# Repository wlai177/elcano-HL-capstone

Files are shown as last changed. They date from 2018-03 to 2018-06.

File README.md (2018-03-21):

View this project on [CADLAB.io](https://cadlab.io/node/765). 

# elcano-HL-capstone
Repo for the Elcano high-level redesign project (BEE capstone project)

The Elcano High-Level system is responsible for setting a desired vehicle speed and direction based on localization, pathfinding, and obstacle detection. The Low-Level system then has the job of making the vehicle execute the desired commands. At present, the High-Level system is partitioned among several processors:
· C7 (Raspberry Pi) processes visual information
· C6 (Arduino Mega) localization based on GPS, speed, and INU
· C5 (Arduino Micro) Lidar/sonar obstacle detection
· C4 (Arduino Mega) computes path from digital map
· C3 (Arduino Micro) processes all data and sends instructions to Low-Level

The High-Level Redesign project seeks to port the C6, C4, and C3 processors to a single Arduino DUE. The new processor is designated as the C643 processor and has the following features:
· Elcano Low-Level Backwards Compatibility
· Simplified Serial Communication
· Single Processor Operation
· Arduino IDE Friendly
· Smaller Footprint
· CAN Bus Support
· 32-bit processing

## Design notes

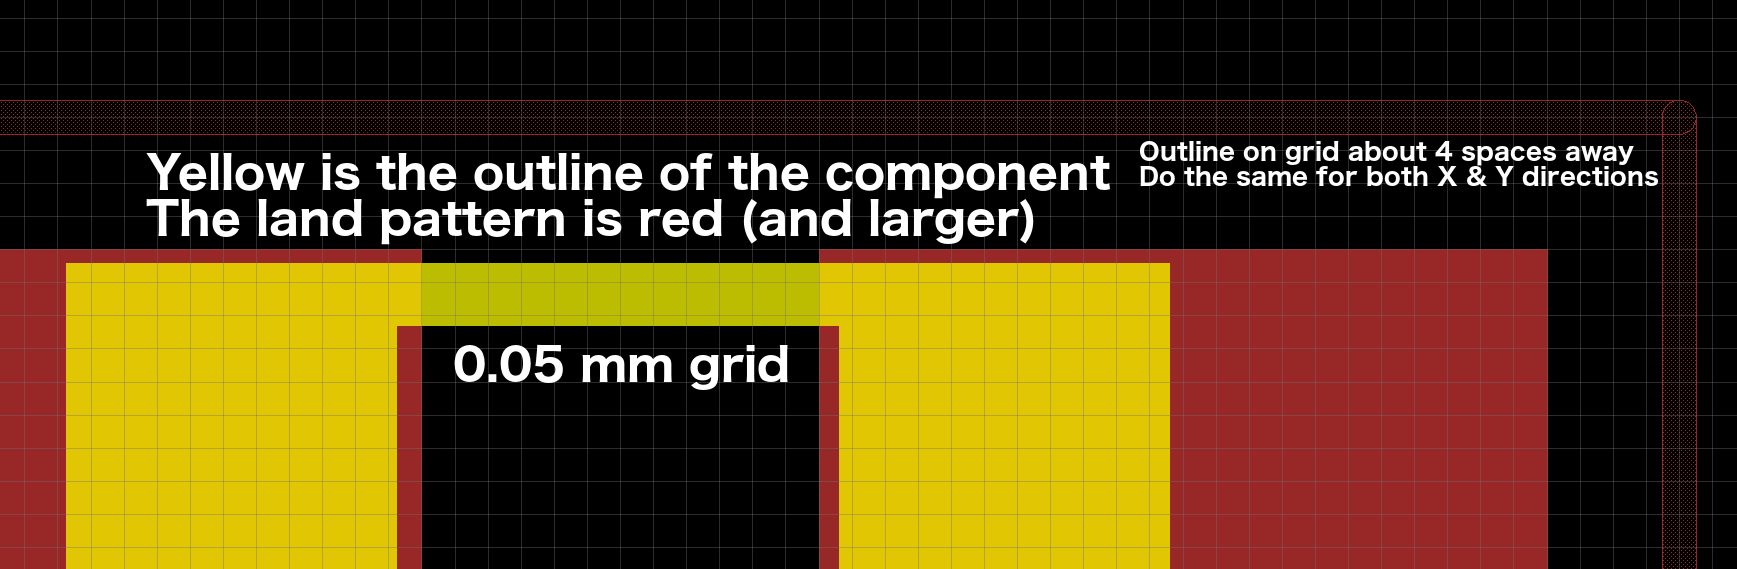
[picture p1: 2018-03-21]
hardware/EAGLE/New Eagle Libraries/SparkFun-Eagle-Libraries-master/images/CourtyardExcess.png

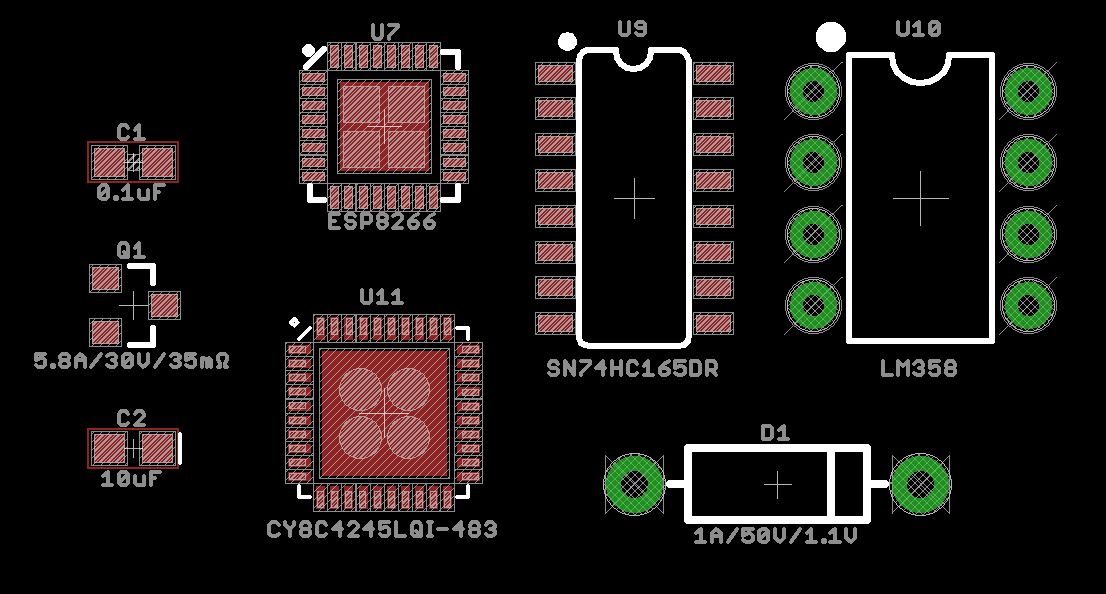
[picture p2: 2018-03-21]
hardware/EAGLE/New Eagle Libraries/SparkFun-Eagle-Libraries-master/images/FootprintExample.png

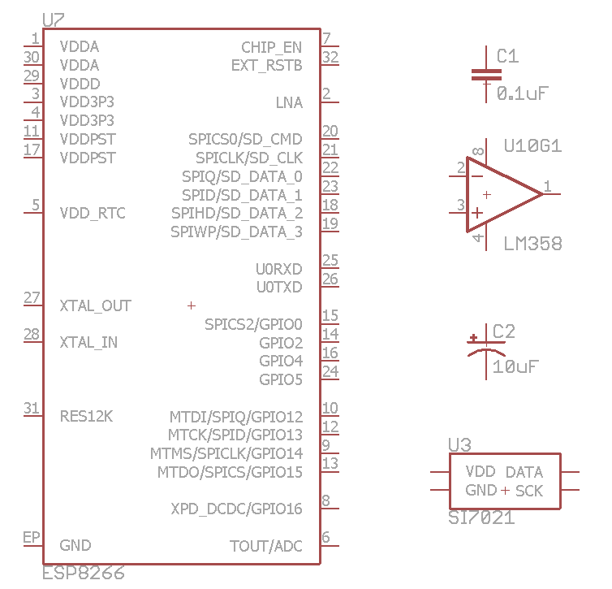
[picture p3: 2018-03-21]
hardware/EAGLE/New Eagle Libraries/SparkFun-Eagle-Libraries-master/images/SymbolExample.png

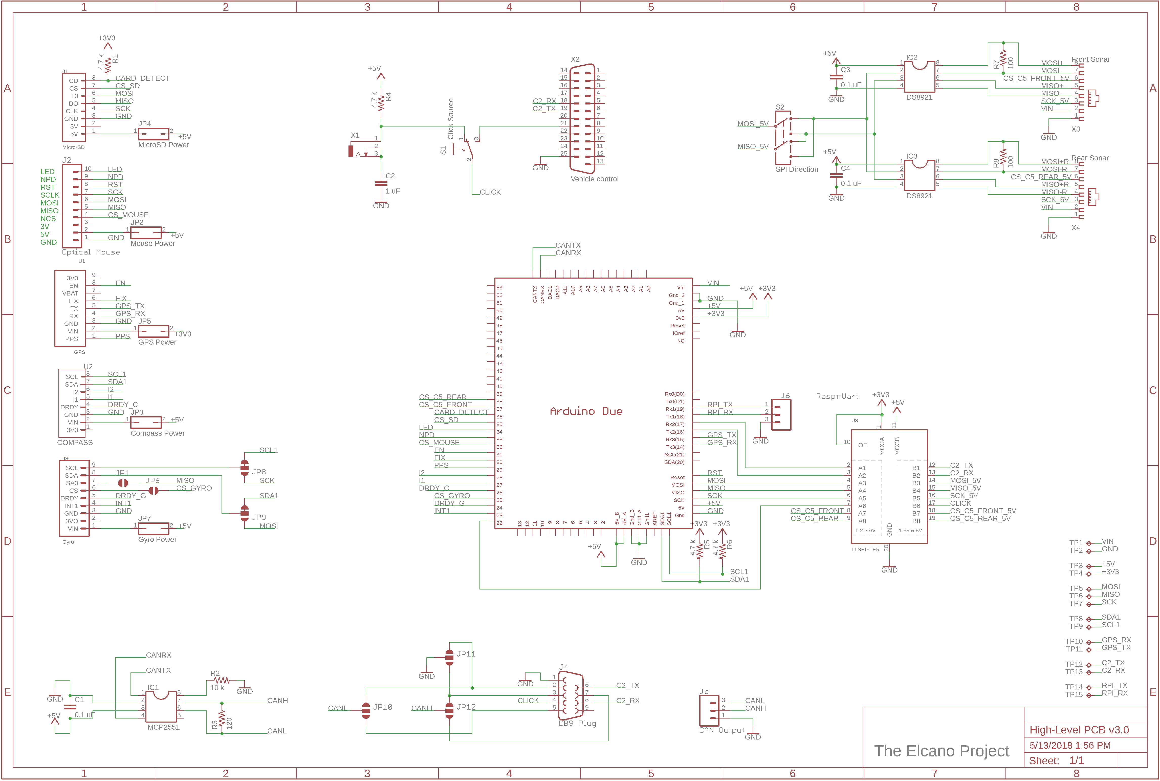
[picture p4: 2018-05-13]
hardware/HL v3 sch - May 13.png

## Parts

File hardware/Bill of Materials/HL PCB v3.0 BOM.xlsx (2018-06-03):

 | Elcano High-Level Bill of Materails
 | High-level PCB v3.0
 | 2018-06-01
# | Item | Value | Quantity | Reference Designator | Notes
1 | Resistor | 4.7 kΩ | 4 | R1 R4 R5 R6
2 | Resistor | 10 kΩ | 1 | R2
3 | Resistor | 120 Ω | 1 | R3 | Optional depending on CAN bus application
4 | Resistor | 100 Ω | 2 | R7 R8
5 | Capacitor | 0.1 uF | 3 | C1 C3 C4
6 | Capacitor | 1 uF | 1 | C2
7 | MCP2551 | - | 1 | IC1 | CAN Bus tranciever
8 | DS8921 | - | 1 | IC2 IC3 | Differential Line Driver and Receiver Pair
9 | Arduino Due | - | 1 | - | https://store.arduino.cc/usa/arduino-due
10 | MicroSD Breakout | - | 1 | J1 | https://www.adafruit.com/product/254
11 | Optical Mouse Sensor | - | 1 | J2 | http://ardupilot.org/copter/docs/common-mouse-based-optical-flow-sensor-adns3080.html
12 | GPS Breakout | - | 1 | U1 | https://www.adafruit.com/product/746
13 | Compass Breakout | - | 1 | U2 | https://www.adafruit.com/product/1120
14 | Gyro Breakout | - | 1 | J3 | https://www.adafruit.com/product/1032
15 | TXS0108E Breakout | - | 1 | - | Logic Level Shifter (5V to 3.3V)
16 | DB9 Male Connector | - | 1 | J4
17 | DB25 Male Connector | - | 1 | X2
18 | 2.5mm Audio Jack | - | 1 | X1
19 | Phoenix Terminal Connector | - | 1 | J5 | Three terminal
20 | RJ45 Connector | - | 2 | X3 X4
21 | SPDT Switch | - | 1 | S1
22 | DPDT Switch | - | 1 | S2
23 | Test Points | - | 15 | TP1-15
24 | MicroSD Card | - | 1 | -
25 | GPS SMA to uFL Adapter | - | 1 | - | Optional
26 | GPS Antenna | - | 1 | - | Optional
27 | Jumpers | - | 5 | -
28 | Female Headers | - | As Required | -
29 | Male Headers | - | As Required | -
30 | 2 Row Headers | - | As Required | -
31 | IC Sockets | - | 3 | -
32 | 7/16" Standoff | - | 8 | -
33 | #2-56 Nuts | - | 8 | -
34 | #2-56 x 3/4 Screws | - | 8 | -

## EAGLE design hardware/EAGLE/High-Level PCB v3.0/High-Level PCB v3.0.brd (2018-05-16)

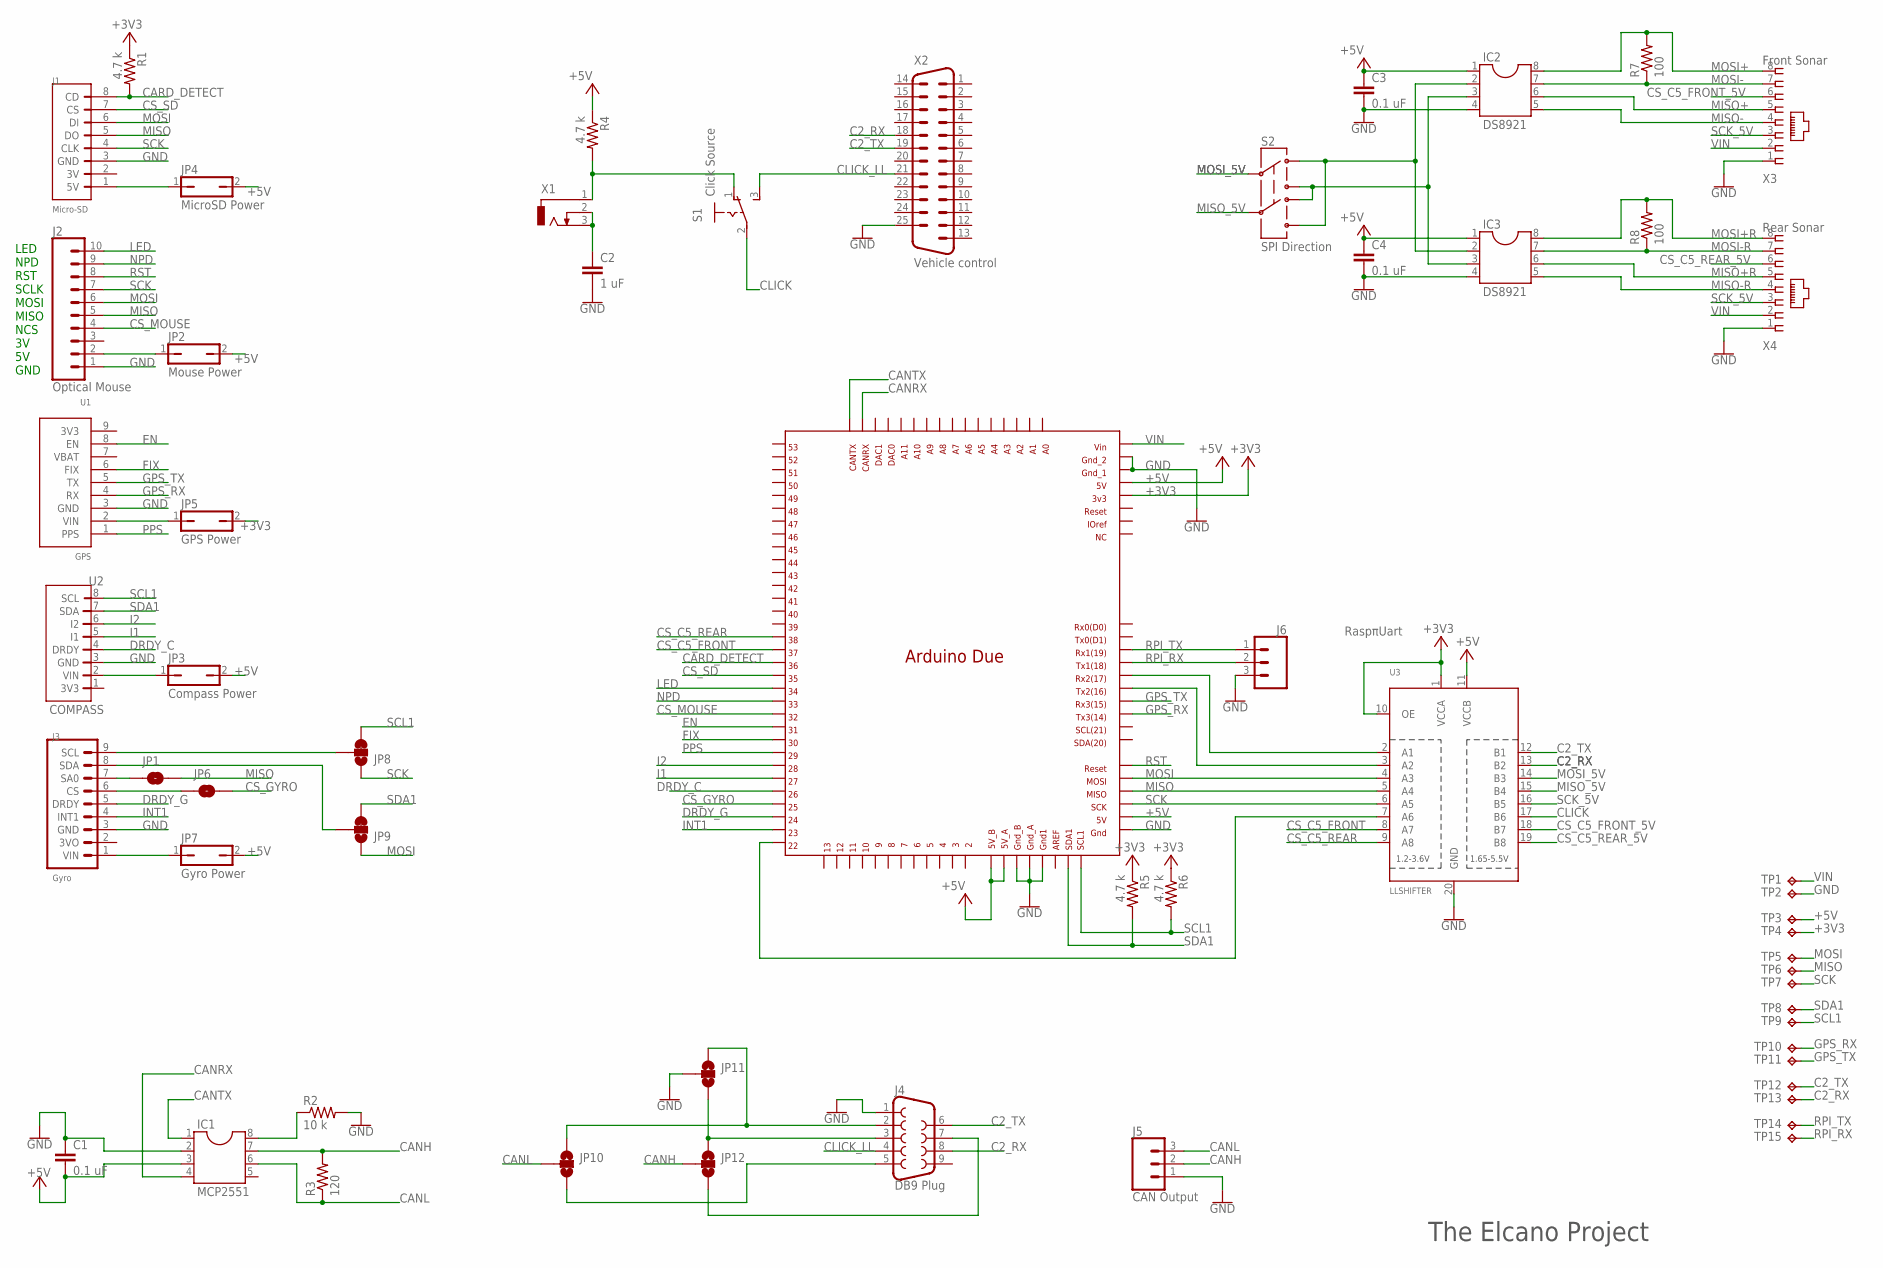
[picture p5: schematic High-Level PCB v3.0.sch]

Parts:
C1, C3, C4: 0.1 uF; C2.5-5
C2: 1 uF; C2.5-5
IC1: MCP2551; DIL08
IC2, IC3: DS8921; DIL08
J1: Micro-SD; ELSDCARD
J2: Optical Mouse; 1X10
J3: Gyro; ELGYRO
J4: DB9 Plug; DB9_MALE
J5: CAN Output; SCREWTERMINAL-5MM-3
J6: RaspπUart; 1X03
JP1, JP6: JUMPER-SMT_2_NO_SILK; SMT-JUMPER_2_NO_SILK
JP2: Mouse Power; JP1
JP3: Compass Power; JP1
JP4: MicroSD Power; JP1
JP5: GPS Power; JP1
JP7: Gyro Power; JP1
JP8, JP9: JUMPER-SMT_3_1-NC_TRACE_SILK; SMT-JUMPER_3_1-NC_TRACE_SILK
JP10, JP11, JP12: JUMPER-SMT_3_NO_SILK; SMT-JUMPER_3_NO_SILK
MCU1: DUE(NORMAL)
R1, R4, R5, R6: 4.7 k; 0204/7
R2: 10 k; 0204/7
R3: 120; 0204/7
R7, R8: 100; 0204/7
S1: Click Source; SP_ELSWITCH
S2: SPI Direction; DPDT
TP1, TP2, TP3, TP4, TP5, TP6, TP7, TP8, TP9, TP10, TP11, TP12, TP13, TP14, TP15: TPPAD1-17; P1-17
U1: GPS; ELGPS
U2: COMPASS; ELCOMPASS
U3: LLSHIFTER; ELSHIFTER
X1: 2.5MMJACK
X2: Vehicle control; M25H
X3: Front Sonar; RJ45-NO-SHIELD
X4: Rear Sonar; RJ45-NO-SHIELD

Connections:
+3V3: JP5.2, MCU1.3V3, R1.1, R5.1, R6.1, TP4.TP, U3.1 (VCCA), U3.10 (OE)
+5V: C1.2, C3.1, C4.1, IC1.3, IC2.1, IC3.1, JP2.2, JP3.2, JP4.2, JP7.2, MCU1.5V, MCU1.5V_A, MCU1.5V_B, MCU1.GND_ICSP, R4.1, TP3.TP, U3.11 (VCCB)
C2_RX: J4.8, TP13.TP, U3.13 (B2), X2.18
C2_TX: J4.6, TP12.TP, U3.12 (B1), X2.19
CANH: IC1.7, J5.2, JP12.2, R3.2
CANL: IC1.6, J5.3, JP10.2, R3.1
CANRX: IC1.4, MCU1.CANRX
CANTX: IC1.1, MCU1.CANTX
CARD_DETECT: J1.8 (CD), MCU1.36, R1.2
CLICK: S1.2, U3.17 (B6)
CLICK_LL: J4.4, S1.3 (S), X2.21
CS_C5_FRONT: MCU1.37, U3.8 (A7)
CS_C5_FRONT_5V: U3.18 (B7), X3.6
CS_C5_REAR: MCU1.38, U3.9 (A8)
CS_C5_REAR_5V: U3.19 (B8), X4.6
CS_GYRO: JP6.2, MCU1.25
CS_MOUSE: J2.4, MCU1.32
CS_SD: J1.7 (CS), MCU1.35
DRDY_C: MCU1.26, U2.4 (DRDY)
DRDY_G: J3.5 (DRDY), MCU1.24
EN: MCU1.31, U1.8 (EN)
FIX: MCU1.30, U1.6 (FIX)
GND: C1.1, C2.2, C3.2, C4.2, IC1.2, IC2.4, IC3.4, J1.3 (GND), J2.1, J3.3 (GND), J4.1, J5.1, J6.3, JP11.2, MCU1.5V_ICSP, MCU1.GND1, MCU1.GND_1, MCU1.GND_2, MCU1.GND_A, MCU1.GND_B, R2.2, TP2.TP, U1.3 (GND), U2.3 (GND), U3.20 (GND), X2.25, X3.1, X4.1
GPS_RX: MCU1.TX3, TP10.TP, U1.4 (RX)
GPS_TX: MCU1.RX3, TP11.TP, U1.5 (TX)
I1: MCU1.27, U2.5 (I1)
I2: MCU1.28, U2.6 (I2)
INT1: J3.4 (INT1), MCU1.23
LED: J2.10, MCU1.34
MISO: J1.5 (DO), J2.5, JP1.2, MCU1.MISO_ICSP, TP6.TP, U3.5 (A4)
MISO+: IC2.6, X3.5
MISO+R: IC3.6, X4.5
MISO-: IC2.5, X3.4
MISO-R: IC3.5, X4.4
MISO_5V: S2.5, U3.15 (B4)
MOSI: J1.6 (DI), J2.6, JP9.1, MCU1.MOSI_ICSP, TP5.TP, U3.4 (A3)
MOSI+: IC2.8, R7.2, X3.8
MOSI+R: IC3.8, R8.2, X4.8
MOSI-: IC2.7, R7.1, X3.7
MOSI-R: IC3.7, R8.1, X4.7
MOSI_5V: S2.2, U3.14 (B3)
unnamed: C2.1, X1.2, X1.3
unnamed: IC2.2, IC3.2, S2.1, S2.6
unnamed: IC2.3, IC3.3, S2.3, S2.4
unnamed: MCU1.TX2, U3.3 (A2)
unnamed: MCU1.RX2, U3.2 (A1)
unnamed: R4.2, S1.1 (O), X1.1
unnamed: JP3.1, U2.2 (VIN)
unnamed: J3.1 (VIN), JP7.1
unnamed: J1.1 (5V), JP4.1
unnamed: J4.3, JP11.3, JP12.1
unnamed: MCU1.22, U3.7 (A6)
unnamed: J2.2, JP2.1
unnamed: JP5.1, U1.2 (VIN)
unnamed: J4.5, JP10.3
unnamed: J4.7, JP12.3
unnamed: IC1.8, R2.1
unnamed: J4.2, JP10.1, JP11.1
unnamed: J3.6 (CS), JP6.1
unnamed: J3.7 (SA0), JP1.1
unnamed: J3.8 (SDA), JP9.2
unnamed: J3.9 (SCL), JP8.2
NPD: J2.9, MCU1.33
PPS: MCU1.29, U1.1 (PPS)
RPI_RX: J6.2 (1), MCU1.TX1, TP15.TP
RPI_TX: J6.1 (2), MCU1.RX1, TP14.TP
RST: J2.8, MCU1.RESET_ICSP
SCK: J1.4 (CLK), J2.7, JP8.1, MCU1.SCK_ICSP, TP7.TP, U3.6 (A5)
SCK_5V: U3.16 (B5), X3.3, X4.3
SCL1: JP8.3, MCU1.SCL1, R6.2, TP9.TP, U2.8 (SCL)
SDA1: JP9.3, MCU1.SDA1, R5.2, TP8.TP, U2.7 (SDA)
VIN: MCU1.VIN, TP1.TP, X3.2, X4.2

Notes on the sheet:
LED NPD RST SCLK MOSI MISO NCS 3V 5V GND
The Elcano Project

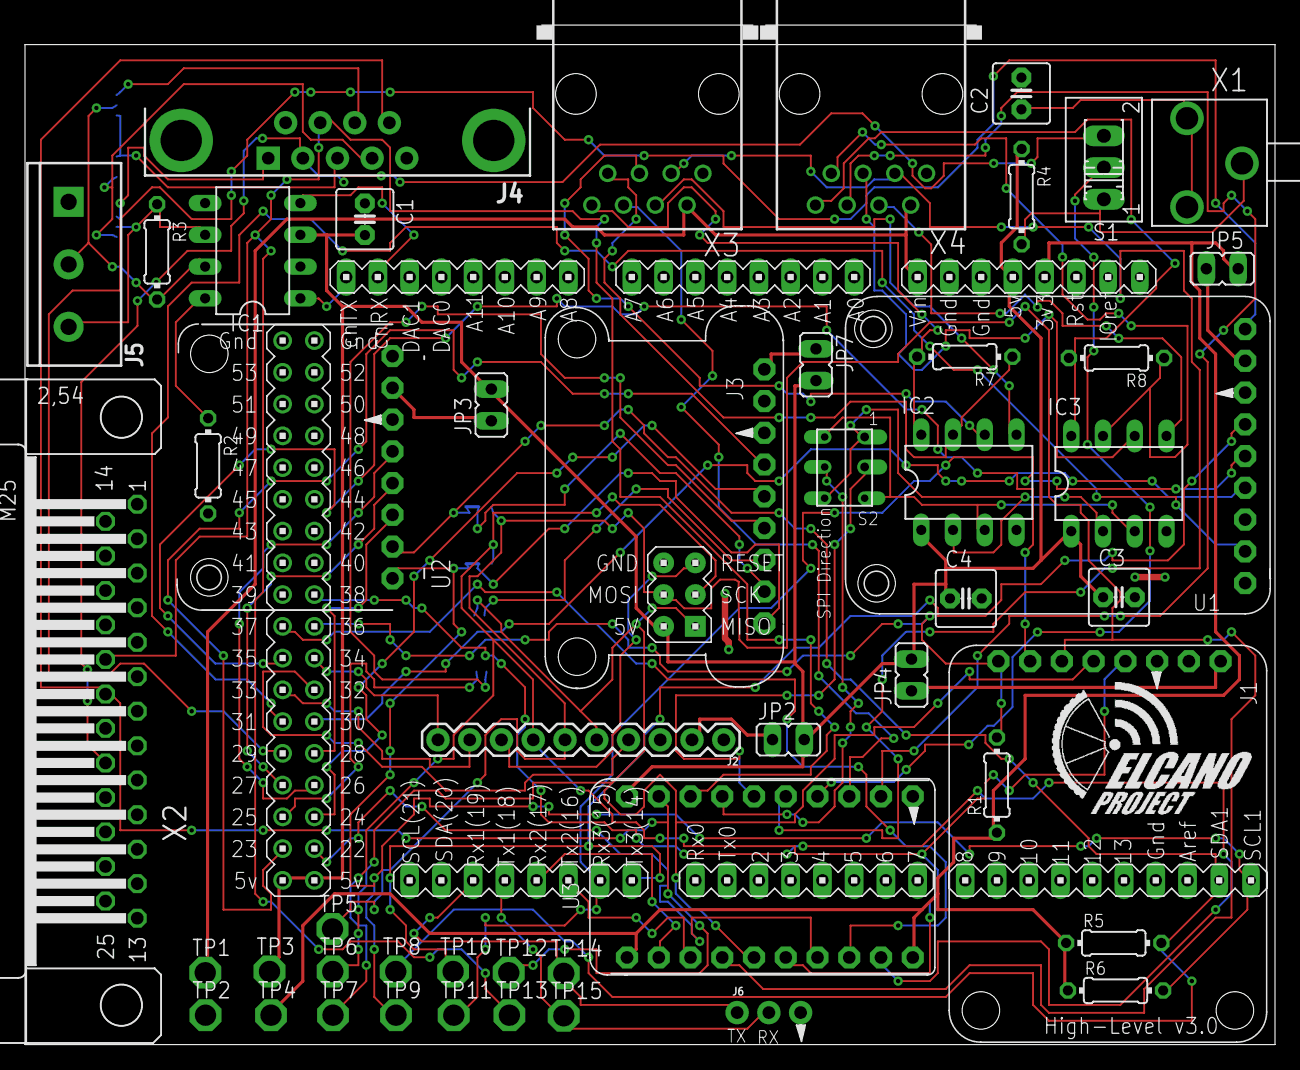
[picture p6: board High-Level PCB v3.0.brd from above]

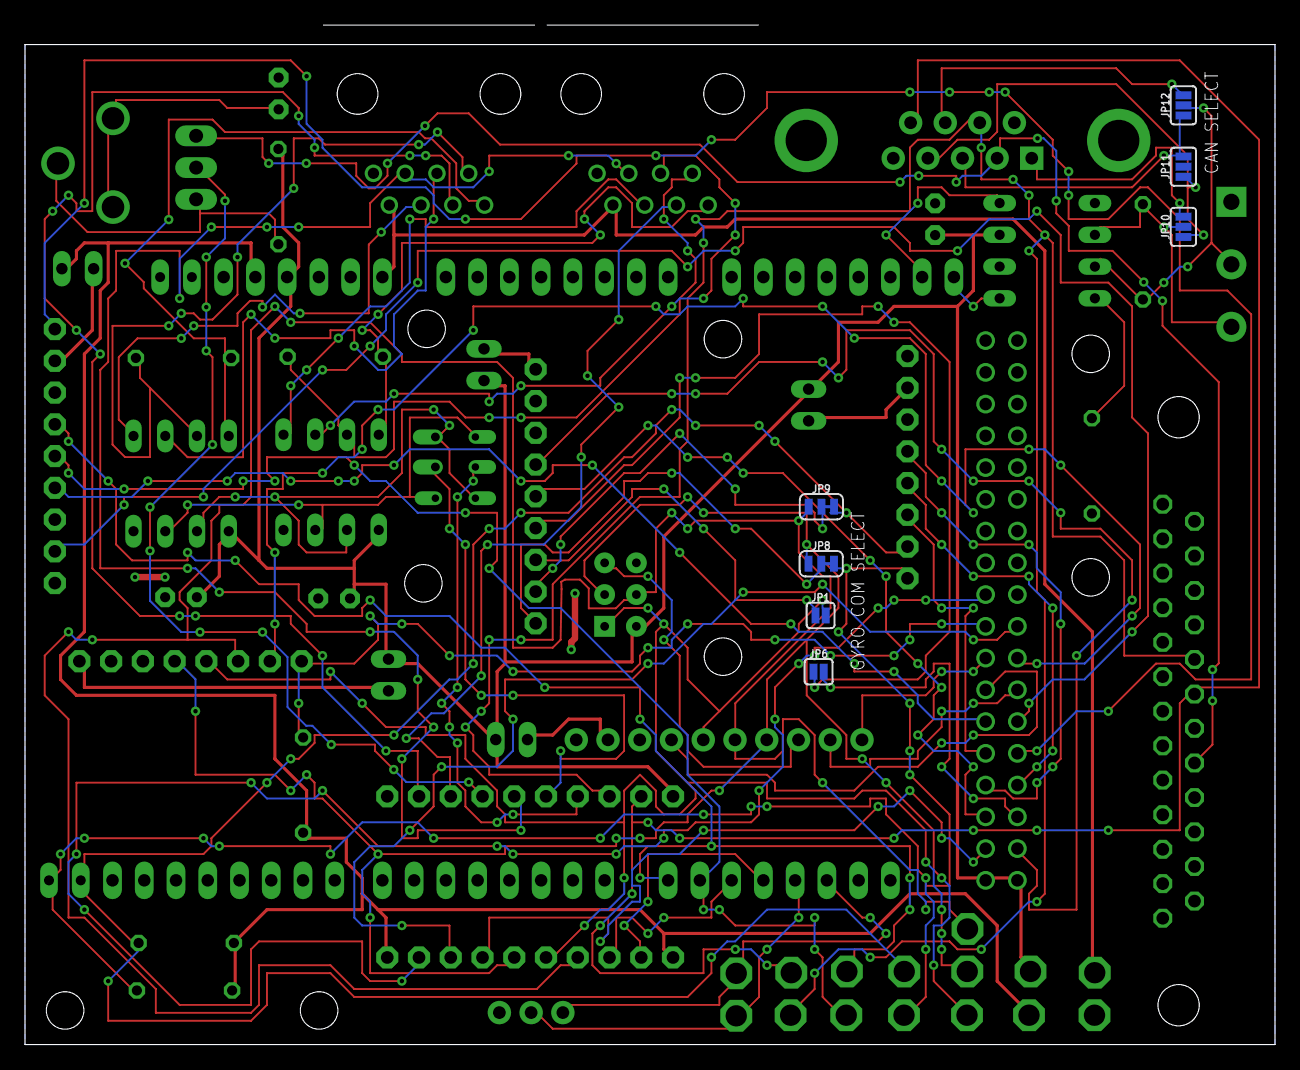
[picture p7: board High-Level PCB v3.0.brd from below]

Board: 2 copper layers, 100.0 x 81.6 mm, 58 parts (7 on the bottom side), 72 nets.

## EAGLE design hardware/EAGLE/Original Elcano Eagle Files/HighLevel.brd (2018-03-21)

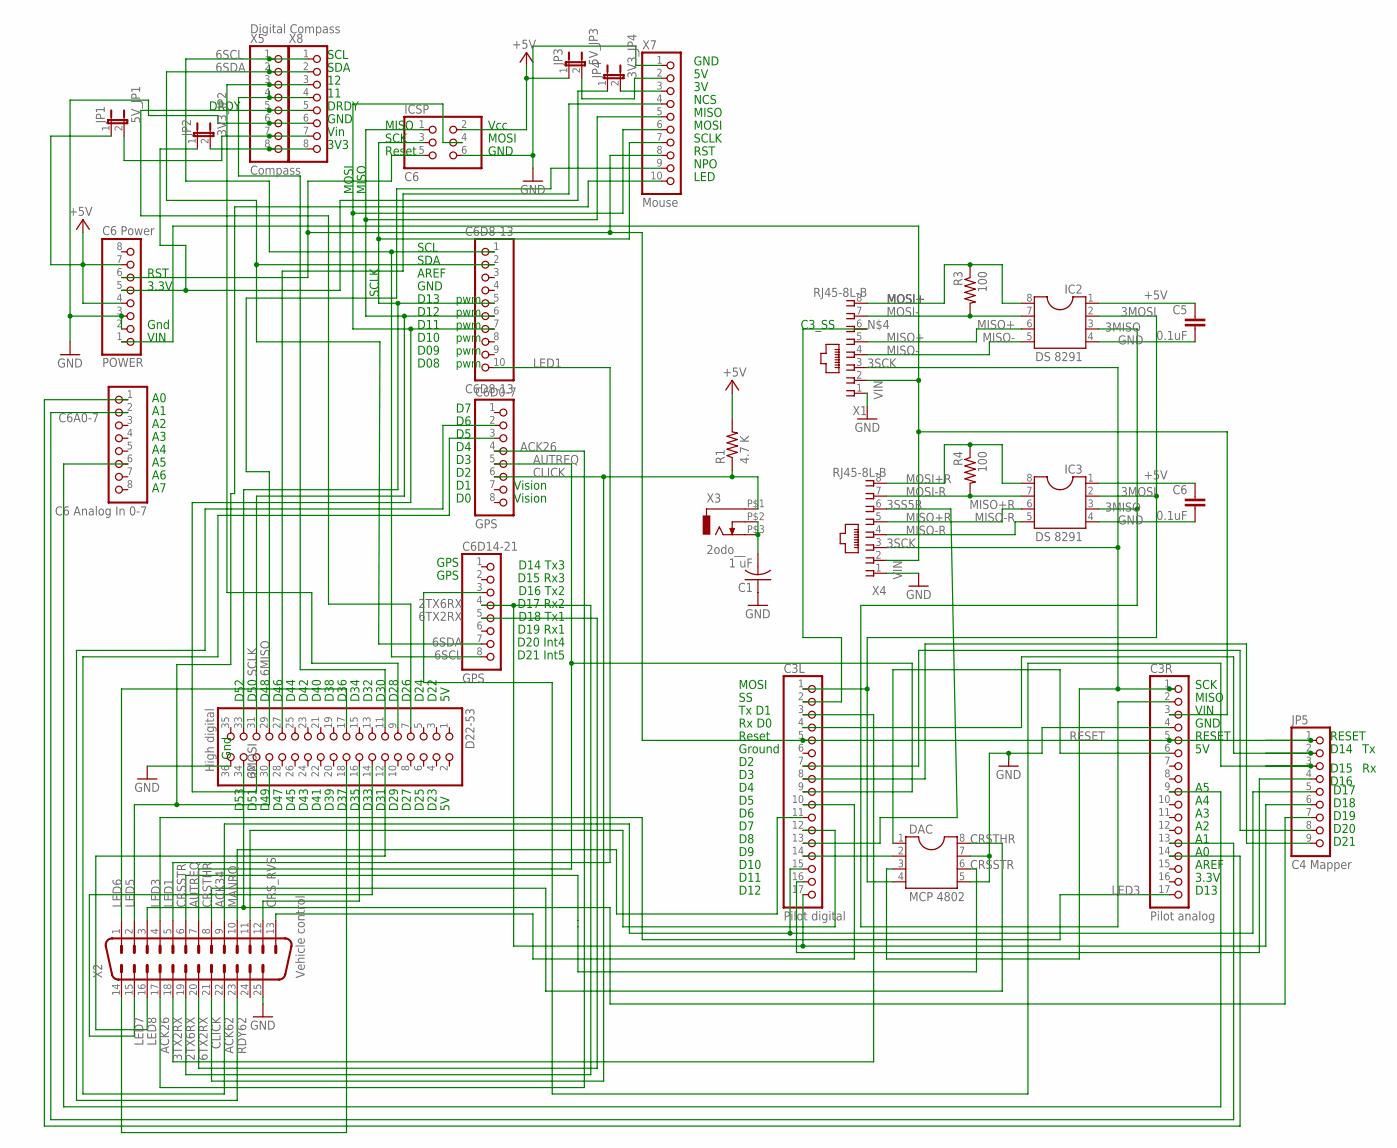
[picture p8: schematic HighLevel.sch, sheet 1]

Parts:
C1: 1 uF; C025-030X050
C3L: Pilot digital; 1X17
C3R: Pilot analog; 1X17
C5, C6: 0.1uF; C2.5-2
C6A0-7: C6 Analog In 0-7; 1X08
C6D0-7, C6D14-21: GPS; 1X08
C6D8-13: C6D8-13; 1X10
D22-53: High digital; 2X18
DAC: MCP 4802; DIL08
IC2, IC3: DS 8291; DIL08
ICSP: C6; 2X03
JP1: 5V_JP1; JP1
JP2: 3V3_JP2; JP1
JP3: 5V_JP3; JP1
JP4: 3V3_JP4; JP1
JP5: C4 Mapper; 1X09
POWER: C6 Power; 1X08
R1: 4.7 K; 0207/10
R3, R4: 100; 0204/5
X1, X4: RJ45-8L-B; RJ45-NO-SHIELD
X2: Vehicle control; M25H
X3: 2odo__; ODO_JACK
X5: Compass; 1X08
X7: Mouse; 1X10
X8: Digital Compass; 1X08

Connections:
2TX6RX: C3L.17, C6D14-21.4, JP5.6, X2.19
3MISO: C3R.2, IC2.3, IC3.3
3MOSI: C3L.1, DAC.4, IC2.2, IC3.2
3SCK: C3R.1, DAC.3, X1.3, X4.3
3SCL: C3L.8, JP5.9
3SDA: C3L.7, JP5.8
3SS5R: C3L.13, X4.6
3SS_DAC: C3L.14, DAC.2
3TX2RX: C3L.3, X2.18
3V3: JP2.1, JP4.1, POWER.5
3VLSM: JP2.2, X5.8, X8.8
5VLSM: JP1.2, X5.7, X8.7
5V_C3: C3R.6, DAC.1
6MISO: C6D8-13.6, D22-53.31, ICSP.1, X7.5
6MOSI: C6D8-13.7, D22-53.32, ICSP.4, X7.6
6SCL: C6D8-13.1, C6D14-21.8, X5.1, X8.1
6SDA: C6D8-13.2, C6D14-21.7, X5.2, X8.2
6TX2RX: C6D14-21.5, X2.20
+5V: C5.1, C6.1, IC2.1, IC3.1, ICSP.2, JP1.1, JP3.1, POWER.4, POWER.7, R1.2
A0: C3R.14, C6A0-7.1
A1: C3R.13, C6A0-7.2
A5: C3R.9, C6A0-7.6
ACK26: C6D0-7.4, X2.17
ACK34: C3L.15, JP5.5, X2.9
ACK43: C3L.16, JP5.4
ACK62: C6D0-7.3, X2.22
AUTREQ: C3L.9, C6D0-7.5, X2.7
CLICK: C6D0-7.6, R1.1, X2.21, X3.P$1 (1)
CRSSTR: DAC.6, X2.6
CRSTHR: DAC.8, X2.8
CRS_RVS: C3L.10, X2.13
D09: D22-53.18, X2.14
DRDY: D22-53.7, X5.5, X8.5
GND: C1.1, C3R.4, C5.2, C6.2, D22-53.36, DAC.5, DAC.7, IC2.4, IC3.4, ICSP.6, POWER.2, POWER.3, X1.1, X2.25, X4.1, X5.6, X7.1, X8.6
I1LSM: D22-53.11, X5.4, X8.4
I2LSM: D22-53.9, X5.3, X8.3
LED1: C6D8-13.10, X2.5
LED3: C3R.17, X2.4
LED4: D22-53.34, JP5.7, X2.3
LED5: D22-53.30, X2.2, X7.10
LED6: D22-53.17, X2.1
LED7: D22-53.14, X2.15
LED8: D22-53.12, X2.16
M3V: JP4.2, X7.3
M5V: JP3.2, X7.2
MANRQ: C3L.11, X2.10
MISO+: IC2.6, X1.5
MISO+R: IC3.6, X4.5
MISO-: IC2.5, X1.4
MISO-R: IC3.5, X4.4
MOSI+: IC2.8, R3.1, X1.8
MOSI+R: IC3.8, R4.1, X4.8
MOSI-: IC2.7, R3.2, X1.7
MOSI-R: IC3.7, R4.2, X4.7
unnamed: C3L.2, X1.6
unnamed: C1.2, X3.P$2 (2), X3.P$3 (3)
NAV_FIX: C6D14-21.3, JP5.3
NCS: D22-53.27, X7.4
NPO: D22-53.29, X7.9
PATH: C3L.4, JP5.2
RDY26: D22-53.16, X2.12
RDY32: C3L.12, X2.11
RDY62: C6D0-7.2, X2.23
RESET: C3L.5, C3R.5, ICSP.5, JP5.1, POWER.6, X7.8
SCLK: C6D8-13.5, D22-53.33, ICSP.3, X7.7
VIN: C3R.3, POWER.1, X1.2, X4.2

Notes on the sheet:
pwm
Gnd
D10
D11
D12
D13
D09
D08
VIN
Rx D0
Tx D1
Reset
Ground
D14 Tx3
D15 Rx3
D16 Tx2
D17 Rx2
D18 Tx1
D19 Rx1
D20 Int4
D21 Int5
MISO
MOSI
SCLK
SCK
Vcc
GND
D52
D22
RST
C3_SS
3.3V
AREF
DRDY
GPS
Vision
D27
D29
D31
D25

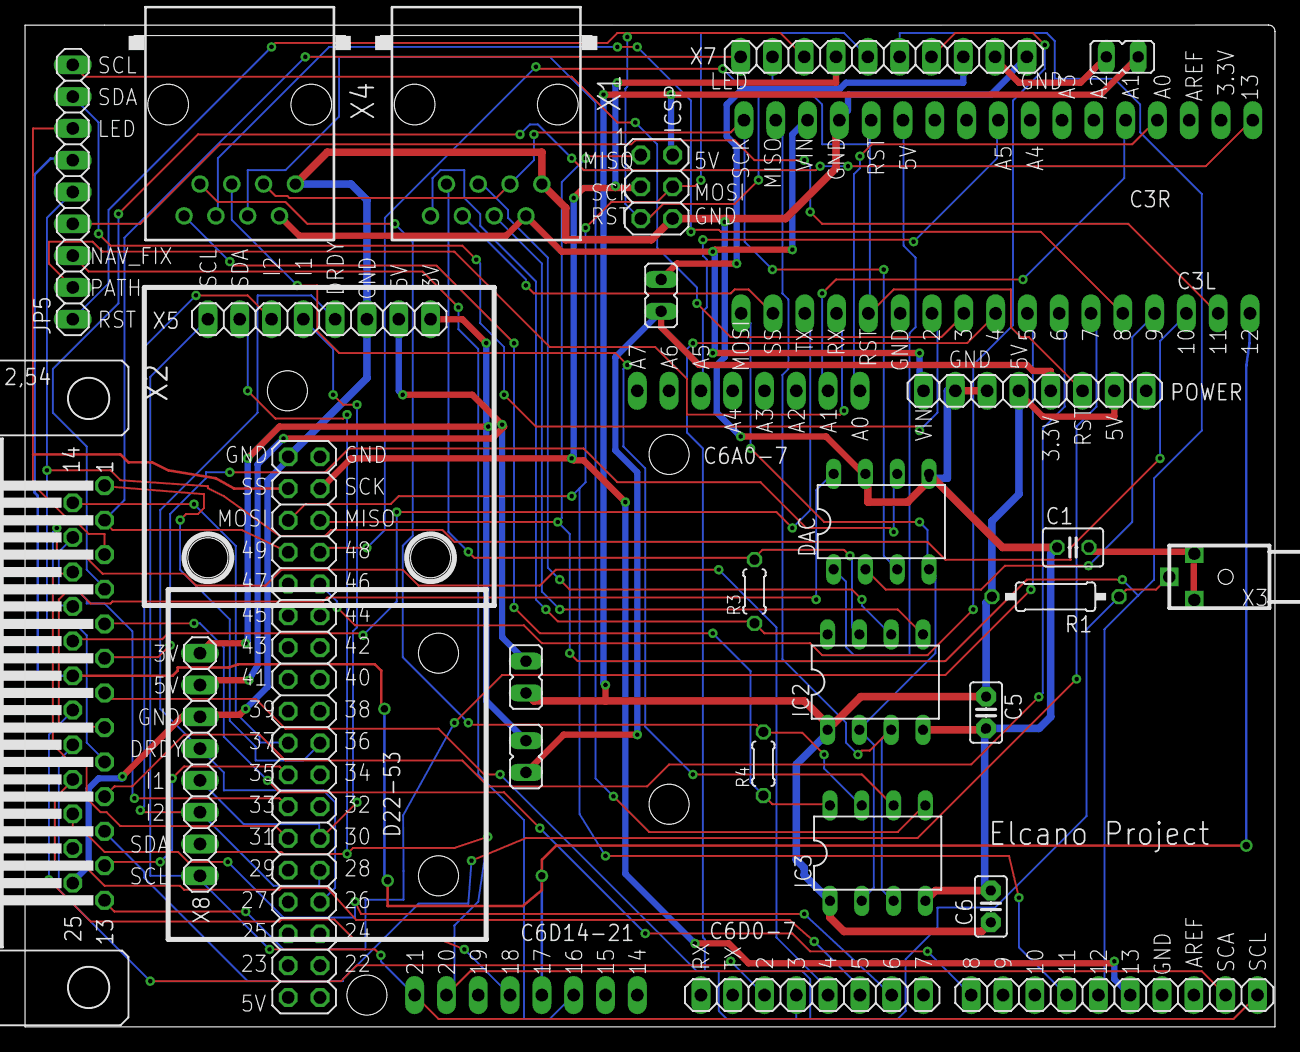
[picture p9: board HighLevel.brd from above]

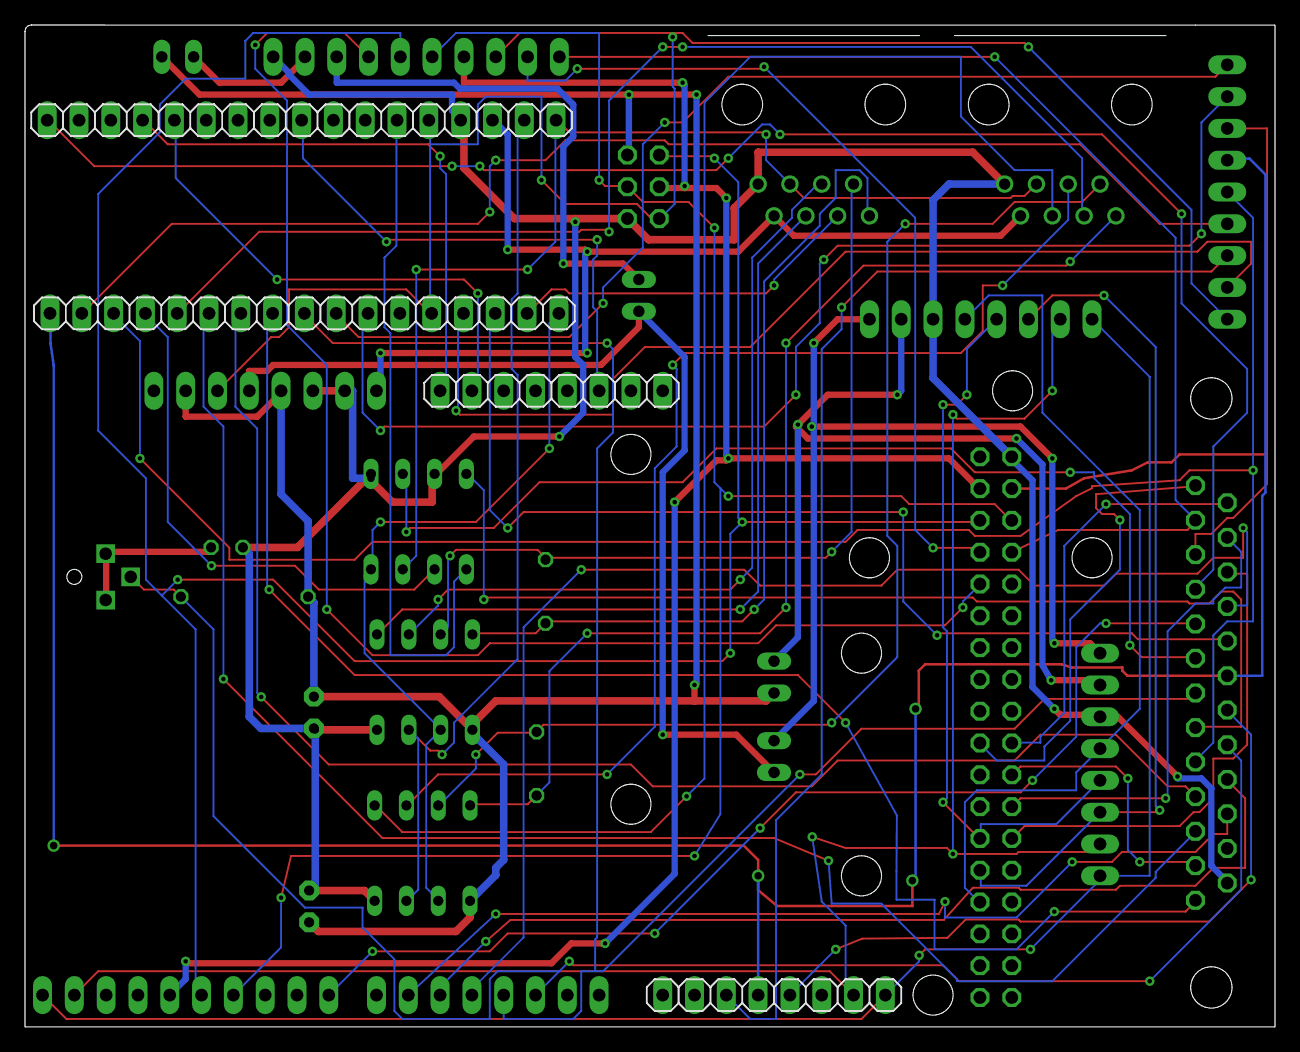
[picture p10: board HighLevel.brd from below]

Board: 2 copper layers, 99.8 x 80.0 mm, 30 parts (4 on the bottom side), 66 nets.

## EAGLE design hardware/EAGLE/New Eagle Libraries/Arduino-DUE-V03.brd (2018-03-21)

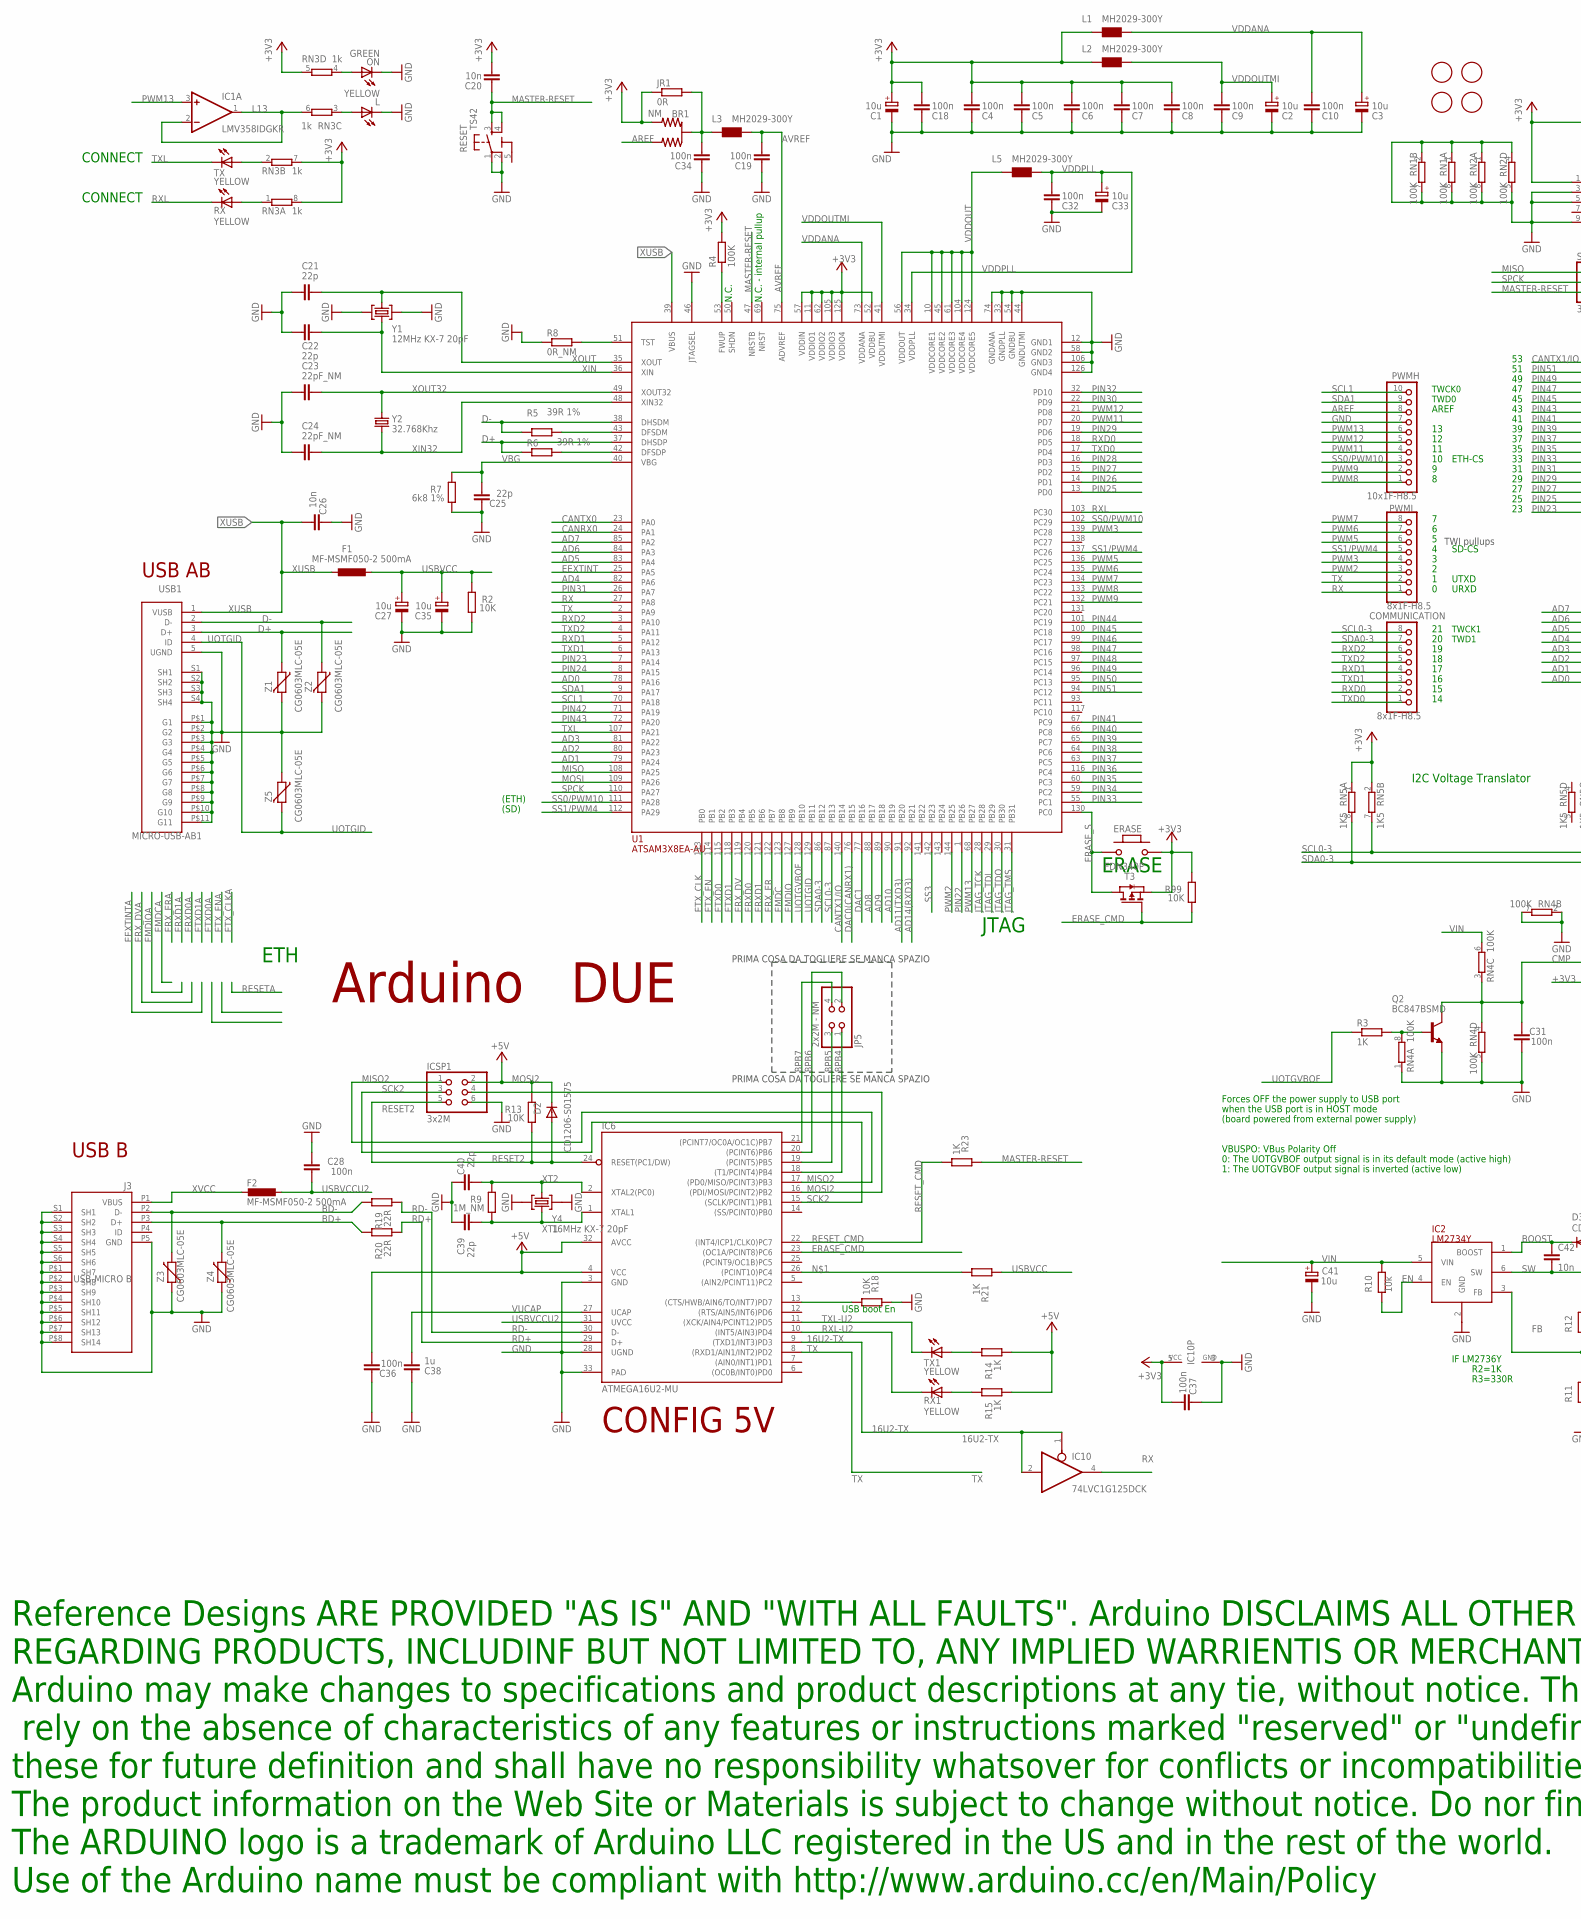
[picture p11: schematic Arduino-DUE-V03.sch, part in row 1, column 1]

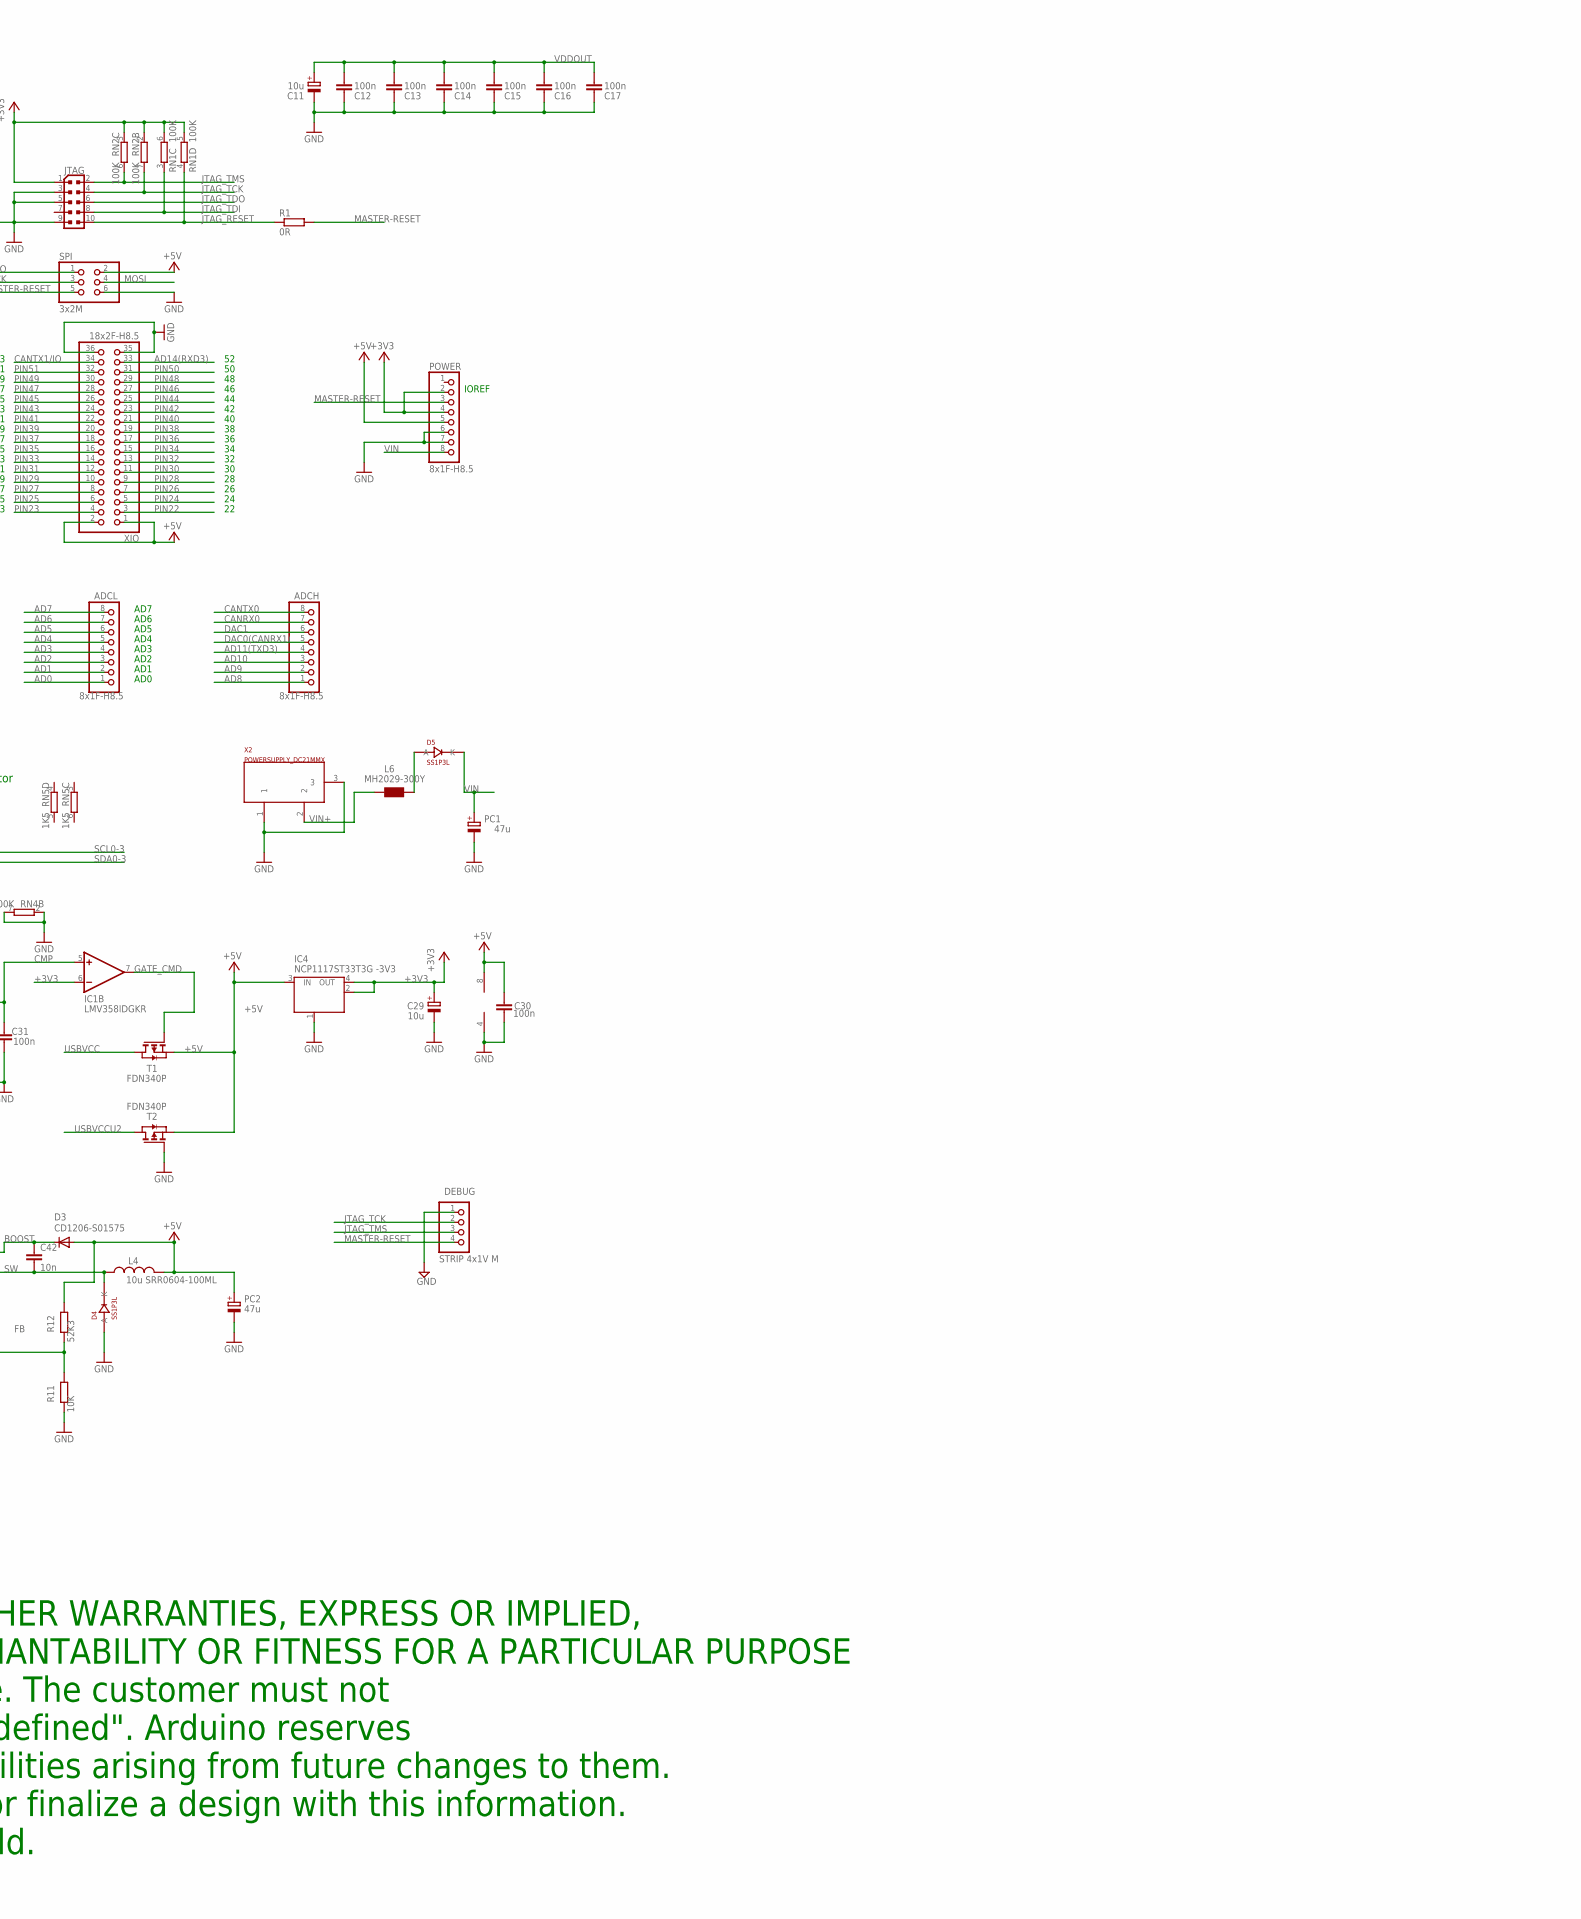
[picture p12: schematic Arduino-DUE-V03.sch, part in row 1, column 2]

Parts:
ADCH: 8x1F-H8.5; 1X08
ADCL: 8x1F-H8.5; 1X08
BR1: NM; J0402
C1, C2, C3, C11, C27, C29, C33, C35, C41: 10u; SMC_B
C4, C5, C6, C7, C8, C9, C10, C12, C13, C14, C15, C16, C17, C18, C19, C28, C30, C31, C32, C34, C36, C37: 100n; C0402
C20, C26: 10n; C0402
C21, C22, C25, C39, C40: 22p; C0402
C23, C24: 22pF_NM; C0402
C38: 1u; C0402
C42: 10n; C0603-ROUND
COMMUNICATION: 8x1F-H8.5; 1X08
D2, D3: CD1206-S01575; MINIMELF
D4, D5: SS1P3L; DO220AAL
DEBUG: STRIP 4x1V M; 1X04
ERASE: MYSMD_PB157; SMD_157SW
F1, F2: MF-MSMF050-2 500mA; L1812
FID1, FID2, FID3, FID4: FIDUCIALMOUNT; FIDUCIA-MOUNT
IC1: LMV358IDGKR; MSOP08
IC2: LM2734Y; SOT23-6
IC4: NCP1117ST33T3G -3V3; SOT223
IC6: ATMEGA16U2-MU; MLF32
IC10: 74LVC1G125DCK; SC70-5
ICSP1: 3x2M; 2X03
J3: USB-MICRO B; CON2_USB_MICRO_B_AT
JP5: 2x2M - NM; 2X02
JR1: 0R; R0402
JTAG: PINHEAD_PINHD-2X5PASSO127; PINHEAD_2X05_127
L: YELLOW; CHIP-LED0805
L1, L2, L3, L5, L6: MH2029-300Y; 0805
L4: 10u SRR0604-100ML; SRR0604
ON: GREEN; CHIP-LED0805
PC1, PC2: 47u; PANASONIC_D
POWER: 8x1F-H8.5; 1X08
PWMH: 10x1F-H8.5; 1X10
PWML: 8x1F-H8.5; 1X08
Q2: BC847BSMD; SOT23
R1: 0R; R0402
R2, R13, R18, R99: 10K; R0402
R3, R14, R15, R21, R23: 1K; R0402
R4: 100K; R0402
R5, R6: 39R 1%; R0402
R7: 6k8 1%; R0603-ROUND
R8: 0R_NM; R0402
R9: 1M_NM; R0402
R10: 10k; R0402
R11: 10K; R0603-ROUND
R12: 52K3; R0603-ROUND
R19, R20: 22R; R0402
RESET: TS42
RN1, RN2, RN4: 100K; CAT16
RN3: 1k; CAY16
RN5: 1K5; CAT16
RX, RX1: YELLOW; CHIP-LED0805
SPI: 3x2M; 2X03
T1, T2, T3: FDN340P; SOT-23
TX, TX1: YELLOW; CHIP-LED0805
U1: ATSAM3X8EA-AU; LQFP144
USB1: MICRO-USB-AB1; MCR-AB1-S-RA-SMT
X2: POWERSUPPLY_DC21MMX; POWERSUPPLY_DC-21MM
XIO: 18x2F-H8.5; 2X18
Y1: 12MHz KX-7 20pF; CRYSTAL-3.2-2.5
Y2: 32.768Khz; RESONATOR_EPSON_FC_145
Y4: 16MHz KX-7 20pF; CRYSTAL-3.2-2.5
Z1, Z2, Z3, Z4, Z5: CG0603MLC-05E; CT/CN0603

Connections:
5-GND: RESET.5 (5-GND)
8PB4: IC6.18 ((T1/PCINT4)PB4), JP5.1
8PB5: IC6.19 ((PCINT5)PB5), JP5.3
8PB6: IC6.20 ((PCINT6)PB6), JP5.2
8PB7: IC6.21 ((PCINT7/OC0A/OC1C)PB7), JP5.4
16U2-TX: IC6.9 ((TXD1/INT3)PD3), IC10.1 (OE), IC10.2 (I)
+3V3: BR1.3 (2), C1.+, C4.2, C5.2, C6.2, C7.2, C8.2, C18.2, C20.2, C29.+, C37.1, ERASE.1, IC1.6 (-IN), IC4.2 (OUT), IC4.4 (OUT), IC10.5 (VCC), JR1.1, JTAG.1, L1.1, L2.1, POWER.2, POWER.4, R4.2, R99.2, RN1.5 (2), RN1.6 (2), RN2.2 (1), RN2.3 (1), RN3.5 (2), RN3.7 (2), RN3.8 (2), RN5.1, RN5.2 (1), T3.2 (S), U1.11 (VDDIO1), U1.52 (VDDBU), U1.57 (VDDIN), U1.62 (VDDIO2), U1.105 (VDDIO3), U1.125 (VDDIO4)
+5V: C30.2, C36.1, D2.C, D3.A, IC1.8 (V+), IC4.3 (IN), IC6.4 (VCC), IC6.32 (AVCC), ICSP1.2, L4.P$2 (2), PC2.+, POWER.5, R12.1, R13.2, R14.1, R15.1, SPI.2, T1.2 (S), T2.2 (S), XIO.1, XIO.2
AD0: ADCL.1, U1.78 (PA16)
AD1: ADCL.2, U1.79 (PA24)
AD2: ADCL.3, U1.80 (PA23)
AD3: ADCL.4, U1.81 (PA22)
AD4: ADCL.5, U1.82 (PA6)
AD5: ADCL.6, U1.83 (PA4)
AD6: ADCL.7, U1.84 (PA3)
AD7: ADCL.8, U1.85 (PA2)
AD8: ADCH.1, U1.88 (PB17)
AD9: ADCH.2, U1.89 (PB18)
AD10: ADCH.3, U1.90 (PB19)
AD11(TXD3): ADCH.4, U1.91 (PB20)
AD14(RXD3): U1.92 (PB21), XIO.33
AREF: BR1.1, PWMH.8
AVREF: C19.2, L3.2, U1.75 (ADVREF)
AVREFL: BR1.2 (C), C34.2, JR1.2, L3.1
BD+: J3.P3 (D+), R20.2, Z4.2
BD-: J3.P2 (D-), R19.2, Z3.2
BOOST: C42.1, D3.C, IC2.1 (BOOST)
CANRX0: ADCH.7, U1.24 (PA1)
CANTX0: ADCH.8, U1.23 (PA0)
CANTX1/IO: U1.140 (PB14), XIO.34
CMP: C31.2, IC1.5 (+IN), Q2.3 (C), RN4.3 (1), RN4.4 (1)
D+: R6.1, U1.37 (DHSDP), USB1.3 (D+), Z1.1
D-: R5.1, U1.38 (DHSDM), USB1.2 (D-), Z2.1
DAC0(CANRX1): ADCH.5, U1.76 (PB15)
DAC1: ADCH.6, U1.77 (PB16)
DTR: IC6.13 ((CTS/HWB/AIN6/TO/INT7)PD7), R18.1
EEXTINT: U1.25 (PA5)
EMDC: U1.123 (PB8)
EMDIO: U1.127 (PB9)
EN: IC2.4 (EN), R10.2
ERASE_CMD: IC6.23 ((OC1A/PCINT8)PC6), R99.1, T3.3 (G)
ERASE_S: ERASE.2, T3.1 (D), U1.130 (PC0)
ERXD0: U1.120 (PB5)
ERXD1: U1.121 (PB6)
ERX_DV: U1.119 (PB4)
ERX_ER: U1.122 (PB7)
ETXD0: U1.115 (PB2)
ETXD1: U1.118 (PB3)
ETX_CLK: U1.113 (PB0)
ETX_EN: U1.114 (PB1)
FB: IC2.3 (FB), R11.1, R12.2
GATE_CMD: IC1.7 (OUT), T1.3 (G)
GND: C1.-, C2.-, C3.-, C4.1, C5.1, C6.1, C7.1, C8.1, C9.1, C10.1, C11.-, C12.1, C13.1, C14.1, C15.1, C16.1, C17.1, C18.1, C19.1, C21.2, C22.2, C23.2, C24.2, C25.2, C26.2, C27.-, C28.2, C29.-, C30.1, C31.1, C32.1, C33.-, C34.1, C35.-, C36.2, C37.2, C38.2, C39.2, C40.2, C41.-, D4.P$2 (A), DEBUG.1, IC1.4 (V-), IC2.2 (GND), IC4.1 (GND/ADJ), IC6.3 (GND), IC6.28 (UGND), IC6.33 (PAD), IC10.3 (GND), ICSP1.6, J3.P5 (GND), J3.P$1 (SH7), J3.P$2 (SH8), J3.P$3 (SH9), J3.P$4 (SH10), J3.P$5 (SH11), J3.P$6 (SH12), J3.P$7 (SH13), J3.P$8 (SH14), J3.S1 (SH1), J3.S2 (SH2), J3.S3 (SH3), J3.S4 (SH4), J3.S5 (SH5), J3.S6 (SH6), JTAG.3, JTAG.5, JTAG.9, L.C, ON.C, PC1.-, PC2.-, POWER.6, POWER.7, PWMH.7, Q2.2 (E), R2.1, R7.1, R8.1, R11.2, R18.2, RESET.1, RESET.2, RN1.1, RN1.2 (1), RN1.7 (2), RN1.8 (2), RN2.1, RN2.4 (1), RN2.5 (2), RN2.8 (2), RN4.1, RN4.2 (1), RN4.5 (2), RN4.7 (2), SPI.6, T2.3 (G), U1.12 (GND1), U1.33 (GNDPLL), U1.44 (GNDUTMI), U1.46 (JTAGSEL), U1.54 (GNDBU), U1.58 (GND2), U1.74 (GNDANA), U1.106 (GND3), U1.126 (GND4), USB1.5 (UGND), USB1.P$1 (G1), USB1.P$2 (G2), USB1.P$3 (G3), USB1.P$4 (G4), USB1.P$5 (G5), USB1.P$6 (G6), USB1.P$7 (G7), USB1.P$8 (G8), USB1.P$9 (G9), USB1.P$10 (G10), USB1.P$11 (G11), USB1.S1 (SH1), USB1.S2 (SH2), USB1.S3 (SH3), USB1.S4 (SH4), X2.1, X2.3, XIO.35, XIO.36, Y1.2 (GND), Y1.4 (GND), Y4.2 (GND), Y4.4 (GND), Z1.2, Z2.2, Z3.1, Z4.1, Z5.1
JTAG_RESET: JTAG.10, R1.1, RN1.4 (1)
JTAG_TCK: DEBUG.2, JTAG.4, RN2.7 (2), U1.28 (PB28)
JTAG_TDI: JTAG.8, RN1.3 (1), U1.29 (PB29)
JTAG_TDO: JTAG.6, U1.30 (PB30)
JTAG_TMS: DEBUG.3, JTAG.2, RN2.6 (2), U1.31 (PB31)
L13: IC1.1 (OUT), IC1.2 (-IN), RN3.6 (2)
MASTER-RESET: C20.1, DEBUG.4, POWER.3, R1.2, R23.2, RESET.3, RESET.4, SPI.5, U1.47 (NRSTB)
MISO: SPI.1, U1.108 (PA25)
MISO2: IC6.17 ((PD0/MISO/PCINT3)PB3), ICSP1.1
MOSI: SPI.4, U1.109 (PA26)
MOSI2: IC6.16 ((PDI/MOSI/PCINT2)PB2), ICSP1.4
unnamed: IC6.26 ((PCINT10)PC4), R21.1
unnamed: L.A, RN3.3 (1)
unnamed: ON.A, RN3.4 (1)
unnamed: R15.2, RX1.A
unnamed: R8.2, U1.51 (TST)
unnamed: Q2.1 (B), R3.2, RN4.8 (2)
unnamed: R4.1, U1.53 (FWUP)
unnamed: D5.P$2 (A), L6.1
unnamed: R5.2, U1.43 (DFSDM)
unnamed: R6.2, U1.42 (DFSDP)
unnamed: R14.2, TX1.A
unnamed: RN3.1, RX.A
unnamed: RN3.2 (1), TX.A
PIN22: U1.1 (PB26), XIO.3
PIN23: U1.7 (PA14), XIO.4
PIN24: U1.8 (PA15), XIO.5
PIN25: U1.13 (PD0), XIO.6
PIN26: U1.14 (PD1), XIO.7
PIN27: U1.15 (PD2), XIO.8
PIN28: U1.16 (PD3), XIO.9
PIN29: U1.19 (PD6), XIO.10
PIN30: U1.22 (PD9), XIO.11
PIN31: U1.26 (PA7), XIO.12
PIN32: U1.32 (PD10), XIO.13
PIN33: U1.55 (PC1), XIO.14
PIN34: U1.59 (PC2), XIO.15
PIN35: U1.60 (PC3), XIO.16
PIN36: U1.116 (PC4), XIO.17
PIN37: U1.63 (PC5), XIO.18
PIN38: U1.64 (PC6), XIO.19
PIN39: U1.65 (PC7), XIO.20
PIN40: U1.66 (PC8), XIO.21
PIN41: U1.67 (PC9), XIO.22
PIN42: U1.71 (PA19), XIO.23
PIN43: U1.72 (PA20), XIO.24
PIN44: U1.101 (PC19), XIO.25
PIN45: U1.100 (PC18), XIO.26
PIN46: U1.99 (PC17), XIO.27
PIN47: U1.98 (PC16), XIO.28
PIN48: U1.97 (PC15), XIO.29
PIN49: U1.96 (PC14), XIO.30
PIN50: U1.95 (PC13), XIO.31
PIN51: U1.94 (PC12), XIO.32
PWM2: PWML.3, U1.144 (PB25)
PWM3: PWML.4, U1.139 (PC28)
PWM5: PWML.6, U1.136 (PC25)
PWM6: PWML.7, U1.135 (PC24)
PWM7: PWML.8, U1.134 (PC23)
PWM8: PWMH.1, U1.133 (PC22)
PWM9: PWMH.2, U1.132 (PC21)
PWM11: PWMH.4, U1.20 (PD7)
PWM12: PWMH.5, U1.21 (PD8)
PWM13: IC1.3 (+IN), PWMH.6, U1.68 (PB27)
RD+: IC6.29 (D+), R20.1
RD-: IC6.30 (D-), R19.1
RESET2: D2.A, IC6.24 (RESET(PC1/DW)), ICSP1.5, R13.1
RESET_CMD: IC6.22 ((INT4/ICP1/CLK0)PC7), R23.1
RX: IC10.4 (O), PWML.1, U1.27 (PA8)
RXD0: COMMUNICATION.2, U1.18 (PD5)
RXD1: COMMUNICATION.4, U1.5 (PA12)
RXD2: COMMUNICATION.6, U1.3 (PA10)
RXL: RX.C, U1.103 (PC30)
RXL-U2: IC6.10 ((INT5/AIN3)PD4), RX1.C
SCK2: IC6.15 ((SCLK/PCINT1)PB1), ICSP1.3
SCL0-3: COMMUNICATION.8, RN5.7 (2), U1.87 (PB13)
SCL1: PWMH.10, U1.70 (PA18)
SDA0-3: COMMUNICATION.7, RN5.8 (2), U1.86 (PB12)
SDA1: PWMH.9, U1.9 (PA17)
SPCK: SPI.3, U1.110 (PA27)
SS0/PWM10: PWMH.3, U1.102 (PC29), U1.111 (PA28)
SS1/PWM4: PWML.5, U1.112 (PA29), U1.137 (PC26)
SS3: U1.142 (PB23)
SW: C42.2, D4.P$1 (K), IC2.6 (SW), L4.P$1 (1)
TX: IC6.8 ((RXD1/AIN1/INT2)PD2), PWML.2, U1.2 (PA9)
TXD0: COMMUNICATION.1, U1.17 (PD4)
TXD1: COMMUNICATION.3, U1.6 (PA13)
TXD2: COMMUNICATION.5, U1.4 (PA11)
TXL: TX.C, U1.107 (PA21)
TXL-U2: IC6.11 ((XCK/AIN4/PCINT12)PD5), TX1.C
UOTGID: U1.129 (PB11), USB1.4 (ID), Z5.2
UOTGVBOF: R3.1, U1.128 (PB10)
USBVCC: C27.+, C35.+, F1.1, R2.2, R21.2, T1.1 (D)
USBVCCU2: C28.1, F2.1, IC6.31 (UVCC), T2.1 (D)
VBG: C25.1, R7.2, U1.40 (VBG)
VDDANA: C3.+, C10.2, L1.2, U1.73 (VDDANA)
VDDOUT: C11.+, C12.2, C13.2, C14.2, C15.2, C16.2, C17.2, L5.1, U1.10 (VDDCORE1), U1.45 (VDDCORE2), U1.56 (VDDOUT), U1.61 (VDDCORE3), U1.104 (VDDCORE4), U1.124 (VDDCORE5)
VDDOUTMI: C2.+, C9.2, L2.2, U1.41 (VDDUTMI)
VDDPLL: C32.2, C33.+, L5.2, U1.34 (VDDPLL)
VIN: C41.+, D5.P$1 (K), IC2.5 (VIN), PC1.+, POWER.8, R10.1, RN4.6 (2)
VIN+: L6.2, X2.2
VUCAP: C38.1, IC6.27 (UCAP)
XIN: C22.1, U1.36 (XIN), Y1.1 (C1)
XIN32: C24.1, U1.48 (XIN32), Y2.P$2 (2)
XOUT: C21.1, U1.35 (XOUT), Y1.3 (C2)
XOUT32: C23.1, U1.49 (XOUT32), Y2.P$1 (1)
XT1: C39.1, IC6.1 (XTAL1), R9.1, Y4.1 (C1)
XT2: C40.1, IC6.2 (XTAL2(PC0)), R9.2, Y4.3 (C2)
XUSB: C26.1, F1.2, U1.39 (VBUS), USB1.1 (VUSB)
XVCC: F2.2, J3.P1 (VBUS)

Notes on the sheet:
TWI pullups
TWCK1
TWD1
IOREF
TWCK0
TWD0
AD1
AD2
AD3
AD4
AD5
AD6
AD0
USB AB
AREF
AD7
SD-CS
Forces OFF the power supply to USB port
when the USB port is in HOST mode
(board powered from external power supply)
N.C.
JTAG
ERASE
CONNECT
VBUSPO: VBus Polarity Off
0: The UOTGVBOF output signal is in its default mode (active high)
1: The UOTGVBOF output signal is inverted (active low)
ETH
UTXD
URXD
(ETH)
(SD)
ETH-CS
I2C Voltage Translator
USB boot En
IF LM2736Y
R2=1K
R3=330R
PRIMA COSA DA TOGLIERE SE MANCA SPAZIO
CONFIG 5V

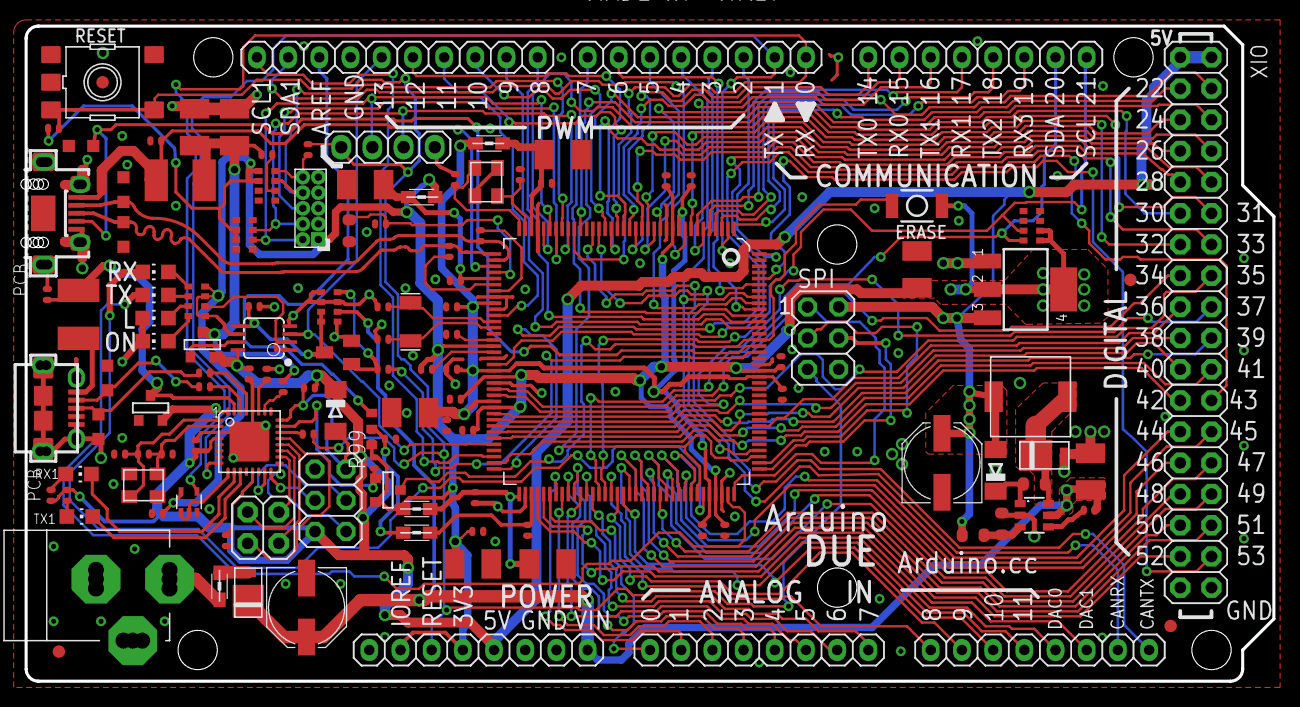
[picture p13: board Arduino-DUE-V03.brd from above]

Board: 2 copper layers, 101.6 x 53.3 mm, 129 parts (0 on the bottom side), 150 nets.

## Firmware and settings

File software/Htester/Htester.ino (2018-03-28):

//#include <Adafruit_L3GD20.h>
#include <Adafruit_L3GD20_U.h>
#include <Adafruit_LSM303.h>
#include <Adafruit_Sensor.h>
#include <Adafruit_GPS.h>


#include <Wire.h>
#include <SPI.h>
#include <SD.h>

//For SD chip
const int chipSelect = 10;

//   GPS for Arduino DUE Test
//   GPS TX to Arduino Due Serial1 RX pin 15
//   GPS RX to Arduino Due Serial1 TX pin 14
#define mySerial Serial1

Adafruit_GPS GPS(&mySerial);

// Set GPSECHO to 'false' to turn off echoing the GPS data to the Serial console
// Set to 'true' if you want to debug and listen to the raw GPS sentences.
#define GPSECHO  true

// this keeps track of whether we're using the interrupt
// off by default!
boolean usingInterrupt = false;

//For Compass
Adafruit_LSM303 lsm;

/**
 * For Gyro Sensor 
 */
// Comment this next line to use SPI
#define USE_I2C

#ifdef USE_I2C
// The default constructor uses I2C
Adafruit_L3GD20 gyro;
#else
// To use SPI, you have to define the pins
#define GYRO_CS 4 // labeled CS
#define GYRO_DO 5 // labeled SA0
#define GYRO_DI 6  // labeled SDA
#define GYRO_CLK 7 // labeled SCL
Adafruit_L3GD20 gyro(GYRO_CS, GYRO_DO, GYRO_DI, GYRO_CLK);
#endif

/*
 * Uncomment to test each module indiviually or all together 
 */
void setup() {
//  SDSetup();
//  GPSSetup();
//  CompassSetup();
//  GyroSetup();

}

/*
 * Uncomment to test each module indiviually or all together 
 */
void loop() {
  //TestSDChip();
  //delay(1000);
  
  //TestGPS();
  //delay(1000);
  
  //TestCompass();
  //delay(1000);
  
  //TestGyro();
  //delay(1000);
}


/*
   MicroSD Setup
*/
void SDSetup() {
  // Open serial communications and wait for port to open:
  Serial.begin(9600);
  while (!Serial) {
    ; // wait for serial port to connect. Needed for native USB port only
  }


  Serial.print("Initializing SD card...");

  // see if the card is present and can be initialized:
  if (!SD.begin(chipSelect)) {
    Serial.println("Card failed, or not present");
    // don't do anything more:
    return;
  }
  Serial.println("card initialized.");
}

/**
   Read and Write to SD Card
*/
void TestSDChip() {
  // make a string for assembling the data to log:
  String dataString = "";

  // read three sensors and append to the string:
  for (int analogPin = 0; analogPin < 3; analogPin++) {
    int sensor = analogRead(analogPin);
    dataString += String(sensor);
    if (analogPin < 2) {
      dataString += ",";
    }
  }

  // open the file. note that only one file can be open at a time,
  // so you have to close this one before opening another.
  File dataFile = SD.open("datalog.txt", FILE_WRITE);

  // if the file is available, write to it:
  if (dataFile) {
    dataFile.println(dataString);
    dataFile.close();
    // print to the serial port too:
    Serial.println(dataString);
  }
  // if the file isn't open, pop up an error:
  else {
    Serial.println("error opening datalog.txt");
  }

}
/**
 * Setup for GPS Module 
 */
void GPSSetup()  {

  // connect at 115200 so we can read the GPS fast enough and echo without dropping chars
  // also spit it out
  Serial.begin(115200);
  Serial.println("Adafruit GPS library basic test!");

  // 9600 NMEA is the default baud rate for Adafruit MTK GPS's- some use 4800
  GPS.begin(9600);
  mySerial.begin(9600);

  // uncomment this line to turn on RMC (recommended minimum) and GGA (fix data) including altitude
  GPS.sendCommand(PMTK_SET_NMEA_OUTPUT_RMCGGA);
  // uncomment this line to turn on only the "minimum recommended" data
  //GPS.sendCommand(PMTK_SET_NMEA_OUTPUT_RMCONLY);
  // For parsing data, we don't suggest using anything but either RMC only or RMC+GGA since
  // the parser doesn't care about other sentences at this time

  // Set the update rate
  GPS.sendCommand(PMTK_SET_NMEA_UPDATE_1HZ);   // 1 Hz update rate
  // For the parsing code to work nicely and have time to sort thru the data, and
  // print it out we don't suggest using anything higher than 1 Hz

  // Request updates on antenna status, comment out to keep quiet
  GPS.sendCommand(PGCMD_ANTENNA);

  // the nice thing about this code is you can have a timer0 interrupt go off
  // every 1 millisecond, and read data from the GPS for you. that makes the
  // loop code a heck of a lot easier!

#ifdef __arm__
  usingInterrupt = false;  //NOTE - we don't want to use interrupts on the Due
#else
  useInterrupt(true);
#endif

  delay(1000);
  // Ask for firmware version
  mySerial.println(PMTK_Q_RELEASE);
}

#ifdef __AVR__
// Interrupt is called once a millisecond, looks for any new GPS data, and stores it
SIGNAL(TIMER0_COMPA_vect) {
  char c = GPS.read();
  // if you want to debug, this is a good time to do it!
#ifdef UDR0
  if (GPSECHO)
    if (c) UDR0 = c;
  // writing direct to UDR0 is much much faster than Serial.print
  // but only one character can be written at a time.
#endif
}

void useInterrupt(boolean v) {
  if (v) {
    // Timer0 is already used for millis() - we'll just interrupt somewhere
    // in the middle and call the "Compare A" function above
    OCR0A = 0xAF;
    TIMSK0 |= _BV(OCIE0A);
    usingInterrupt = true;
  } else {
    // do not call the interrupt function COMPA anymore
    TIMSK0 &= ~_BV(OCIE0A);
    usingInterrupt = false;
  }
}
#endif //#ifdef__AVR__

uint32_t timer = millis();

/**
 * Store and Parse data with the GPS
 */
void TestGPS()                     
{
  // in case you are not using the interrupt above, you'll
  // need to 'hand query' the GPS, not suggested :(
  if (! usingInterrupt) {
    // read data from the GPS in the 'main loop'
    char c = GPS.read();
    // if you want to debug, this is a good time to do it!
    if (GPSECHO)
      if (c) Serial.print(c);
  }

  // if a sentence is received, we can check the checksum, parse it...
  if (GPS.newNMEAreceived()) {
    // a tricky thing here is if we print the NMEA sentence, or data
    // we end up not listening and catching other sentences!
    // so be very wary if using OUTPUT_ALLDATA and trytng to print out data
    //Serial.println(GPS.lastNMEA());   // this also sets the newNMEAreceived() flag to false

    if (!GPS.parse(GPS.lastNMEA()))   // this also sets the newNMEAreceived() flag to false
      return;  // we can fail to parse a sentence in which case we should just wait for another
  }

  // if millis() or timer wraps around, we'll just reset it
  if (timer > millis())  timer = millis();

  // approximately every 2 seconds or so, print out the current stats
  if (millis() - timer > 2000) {
    timer = millis(); // reset the timer

    Serial.print("\nTime: ");
    Serial.print(GPS.hour, DEC); Serial.print(':');
    Serial.print(GPS.minute, DEC); Serial.print(':');
    Serial.print(GPS.seconds, DEC); Serial.print('.');
    Serial.println(GPS.milliseconds);
    Serial.print("Date: ");
    Serial.print(GPS.day, DEC); Serial.print('/');
    Serial.print(GPS.month, DEC); Serial.print("/20");
    Serial.println(GPS.year, DEC);
    Serial.print("Fix: "); Serial.print((int)GPS.fix);
    Serial.print(" quality: "); Serial.println((int)GPS.fixquality);
    if (GPS.fix) {
      Serial.print("Location: ");
      Serial.print(GPS.latitude, 4); Serial.print(GPS.lat);
      Serial.print(", ");
      Serial.print(GPS.longitude, 4); Serial.println(GPS.lon);

      Serial.print("Speed (knots): "); Serial.println(GPS.speed);
      Serial.print("Angle: "); Serial.println(GPS.angle);
      Serial.print("Altitude: "); Serial.println(GPS.altitude);
      Serial.print("Satellites: "); Serial.println((int)GPS.satellites);
    }
  }
}

/**
 * Setup for the Compass module 
 */
void CompassSetup() {
#ifndef ESP8266
  while (!Serial);     // will pause Zero, Leonardo, etc until serial console opens
#endif
  Serial.begin(9600);

  // Try to initialise and warn if we couldn't detect the chip
  if (!lsm.begin())
  {
    Serial.println("Oops ... unable to initialize the LSM303. Check your wiring!");
    while (1);
  }
}

/**
 * Reading Data from the compass 
 */
void TestCompass() {
  lsm.read();
  Serial.print("AX: "); Serial.print((int)lsm.accelData.x); Serial.print(" ");
  Serial.print("AY: "); Serial.print((int)lsm.accelData.y); Serial.print(" ");
  Serial.print("AZ: "); Serial.print((int)lsm.accelData.z); Serial.print(" ");
  Serial.print("MX: "); Serial.print((int)lsm.magData.x);   Serial.print(" ");
  Serial.print("MY: "); Serial.print((int)lsm.magData.y);   Serial.print(" ");
  Serial.print("MZ: "); Serial.println((int)lsm.magData.z); Serial.print(" ");
  delay(100);
}

/*
 * Set up for Gyro Module 
 */
void GyroSetup() {
  Serial.begin(9600);

  // Try to initialise and warn if we couldn't detect the chip
  if (!gyro.begin(gyro.L3DS20_RANGE_250DPS))
    //if (!gyro.begin(gyro.L3DS20_RANGE_500DPS))
    //if (!gyro.begin(gyro.L3DS20_RANGE_2000DPS))
  {
    Serial.println("Oops ... unable to initialize the L3GD20. Check your wiring!");
    while (1);
  }
}

/*
 * Getting the axis point from the gyro 
 */
void TestGyro() {
  gyro.read();
  Serial.print("X: "); Serial.print((int)gyro.data.x);   Serial.print(" ");
  Serial.print("Y: "); Serial.print((int)gyro.data.y);   Serial.print(" ");
  Serial.print("Z: "); Serial.println((int)gyro.data.z); Serial.print(" ");
  delay(100);
}

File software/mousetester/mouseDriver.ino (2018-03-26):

#include "T3080.h"
#include <SPI.h>
T3080 sensor;
typedef unsigned long Time;
void setup() {
sensor.init_1();
Serial.begin(115200);
Serial.println();
SPI.begin();
SPI.setBitOrder(MSBFIRST);
SPI.setDataMode(SPI_MODE3);
SPI.setClockDivider(SPI_CLOCK_DIV16);
sensor.reset();
sensor.init_2();
}
void loop() {
static Time last_reset;
Time now = millis();
sensor.measurement();
delay(500);
}

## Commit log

2018-03-15 Uploaded initial sch
    Baseline sch that was submitted in the Design Doc
    [High-Level PCB v3.0.sch]
2018-03-15 Moved sch to a new folder
    [High-Level PCB v3.0.sch]
2018-03-16 Libraries for the compass sensor
    Libraries for the LSM303 Compass sensor from adafruit
    Product: https://www.adafruit.com/product/1120
2018-03-16 Create sample text
2018-03-21 Added gyro library
2018-03-21 Moved files from OneDrive
    [Arduino-DUE-V03.brd, Arduino-DUE-V03.sch, High-Level PCB v3.0 - SAVE 1.sch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]
2018-03-21 Added image of draft schematic
    Accurate as of March 10th
2018-03-21 Added/Modified schematic images
    For those who don't have Eagle installed, these images will allow you to view the schematics.
2018-03-26 Added library for RJ45 connector
2018-03-28 WireModification
    L3Gd20_U and LSM303DLHC are no longer adafruit standard libraries.
    replaced all instances of Wire with Wire1
    Due can't work with multiple I2C if SCL 1and SDA1 are used. Note SCL1 and SDA1 need pull up resistors.
    [HighLevel-Peripherals_Tester.ino, Htester.ino]
2018-03-29 Added additional header for compass and moved the i2C to other bus
    [High-Level PCB v3.0.sch]
2018-03-29 Fixed pull-up resistors on I2C bus
    [High-Level PCB v3.0.sch]
2018-03-30 Added code to test UART communication
2018-04-05 Added CAN bus chip (MCP2551)
    [High-Level PCB v3.0.sch]
2018-04-06 Added DB9 and terminal block connectors
    [High-Level PCB v3.0.sch]
2018-04-08 Voltage level shifter adafruit
    Removed Sparkfun voltage level shifter and replaced with adafruit's
    [High-Level PCB v3.0.sch]
2018-04-11 Moved some stuff around and re-routed the logic converter chip
    [High-Level PCB v3.0.sch]
2018-04-11 Added Test Points
    [High-Level PCB v3.0.sch]
2018-04-16 Added some changes (see description)
    Added EN for GPS
    Added CD for microSD
    Cleaned up breakout headers
    Need to connect solder jumpers
    [High-Level PCB v3.0.sch]
2018-04-16 Added larger frame
    [High-Level PCB v3.0.sch]
2018-04-16 Added SPI connection for the Gyro
    [High-Level PCB v3.0.sch]
2018-04-16 Re-arranged pin connections on DUE
    [High-Level PCB v3.0.sch]
2018-04-16 Fixed duplicated I2C lines on the gyro header
    [High-Level PCB v3.0.sch]
2018-04-16 Changed "DUE Shield" label to "Arduino Due"
    [High-Level PCB v3.0.sch]
2018-04-17 Added Test Points for +5V and +3V3
    [High-Level PCB v3.0.sch]
2018-04-22 Add files via upload
    FootPrint for AdaFruit GPS.
2018-04-23 Add files via upload
    TXB0108 adafruit footprint.
2018-04-26 Add files via upload
    ADAFRUIT LSM303 COMPASS breakout board footprint.
2018-04-26 footprints
    foot print updates
2018-04-26 Add files via upload
    Added uart connection for raspberrypi
    [High-Level PCB v3.0.sch]
2018-04-26 Add files via upload
    footprint for raspberry pi connection
2018-04-27 raspberry pi foot prints and compass mods. Added tx, rx lines in schematic for raspberry pi
    raspberry pi foot prints and compass mods.
    Added tx, rx lines in schematic for raspberry pi
2018-04-27 Added footprint for new audio jack
2018-04-29 ElCano breakoutboard footprints.
    Contains footprints in one easy to find package.
2018-04-29 added footprints
    Includes footprints for all breakout boards except optical mouse
    [High-Level PCB v3.0.sch]
2018-04-29 Added Micro Sd breakout board.
    Added Micro Sd breakout board.
2018-05-02 Used larger resistor footprints
    [High-Level PCB v3.0.sch]
2018-05-03 Added correct RJ45 footprints
    [High-Level PCB v3.0.sch]
2018-05-03 drill hole changes
    standarized screw hole to 3mm
2018-05-03 Removed second Compass
    [High-Level PCB v3.0.sch]
2018-05-03 due silk screen fix
    fixed hole move silk screening
2018-05-03 changes
    Changed DPDT. Updated with new Due library where the silk screen has been moved.
    Solved drill hole issue with Due library
    [High-Level PCB v3.0.sch]
2018-05-04 Copied sch to backup folder
    [High-Level PCB v3.0 - SAVE 6 footprints.sch]
2018-05-04 Added Board and fixed Test Points
    Added the BRD file and fixed GPS test points and added test points for Raspberry UART
    [High-Level PCB v3.0.brd, High-Level PCB v3.0.sch]
2018-05-04 Started board layout
    [High-Level PCB v3.0.brd]
2018-05-04 breakout holes
    Fixed hole size for the breakout boards. Should be 3mm for all
    [High-Level PCB v3.0.sch]
2018-05-05 100% autoroute success
    [High-Level PCB v3.0.brd]
2018-05-06 Added "Test" folder with a high ground pour board varient
    [Large ground pour test.brd, Large ground pour test.sch]
2018-05-07 Backuped the 100% auto route brd
    [High-Level PCB v3.0 - 100 auto route.brd]
2018-05-08 Added two more autoroute test
    Board 2 looks decent
    [PCB moved parts 2.brd, PCB moved parts 2.sch, PCB moved parts.brd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]
2018-05-09 Tried adding thicker power traces
    Has air wires!
    [PCB moved parts 3.brd, PCB moved parts 3.sch]
2018-05-10 The 3 board has no air wires!
    And it has thick power traces.
    [PCB moved parts 3.brd, PCB moved parts 3.sch]
2018-05-10 Added Gerber files
2018-05-11 Added a silk screen logo
    [PCB moved parts 3.brd]
2018-05-13 Added and moved some silkscreen labels
    [PCB moved parts 3.brd]
2018-05-13 Moved files around
    Current PCB files are moved one level up
    [High-Level PCB v3.0.brd, High-Level PCB v3.0.sch, Large ground pour test.brd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]
2018-05-13 Generated Gerbers
    PCB rendered provided by JLC PCB
    [High-Level PCB v3.0.brd]
2018-05-13 Updated png image of the v3 HL board
    [High-Level PCB v3.0.sch]
2018-05-16 Fixed Click signal and made new gerbers
    Click signals from the low level systems are now tied together.
    [High-Level PCB v3.0.brd, High-Level PCB v3.0.sch]
2018-05-16 Fixed SPST size and generated new Gerbers
    [High-Level PCB v3.0.brd, High-Level PCB v3.0.sch]
2018-05-23 Added a Bill of Materials BOM
    [HL PCB v3.0 BOM.xlsx]
2018-06-03 Updated BOM
    [HL PCB v3.0 BOM.xlsx]

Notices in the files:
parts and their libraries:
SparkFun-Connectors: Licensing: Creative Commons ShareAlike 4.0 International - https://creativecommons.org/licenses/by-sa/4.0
